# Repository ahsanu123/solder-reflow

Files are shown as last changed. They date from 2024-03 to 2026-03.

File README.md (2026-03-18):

<h1 align="center">🌕 SORE V3 - Prototype 1</h1> 
<p align="center">
  <a href="https://github.com/ahsanu123/solder-reflow"> 
   
  </a>
</p>

<p align="center">
  <a href="">
    
  </a>
  <a href="">
    
  </a>
  <a href="">
    
  </a>
  <a href="https://github.com/ahsanu123/solder-reflow/blob/main/LICENSE">
    
  </a>
</p>

## ✏️ SORE - Solder Reflow

🌕 SORE - Solder Reflow,  DIY hot plate use PT100 for temperature sensor controlled with ESP32-S3,
with TFT LCD, programmed in 🦀 Rust with [Slint](https://slint.dev/) as user interface

> Designed With [KICAD](https://www.kicad.org)

<p align="center" style="background-color: white;">
schematic
</p>

## 🏆 WIP For Version 3

> [!NOTE]
> - use esp32-s3
> - use usb jtag and usb serial 
> - try to use power supply module instead of using external adaptor, [Hi-Link](https://www.tokopedia.com/eltech-online/hi-link-3-3v-5v-9v-12v-24v-hi-link-ling-hlk-ac-to-dc-isolation-power-supply-unit-switching-module-catu-daya-adaptor-trafo-all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)
> - add generic lcd spi connector instead of spesific display pinout.
> - use [Slint](https://slint.dev/) for user interface
> - think about how to stack the heater so its not separated, model it with inventor
> - if possible, buy local component only

<details>
 <summary>Sketch</summary>
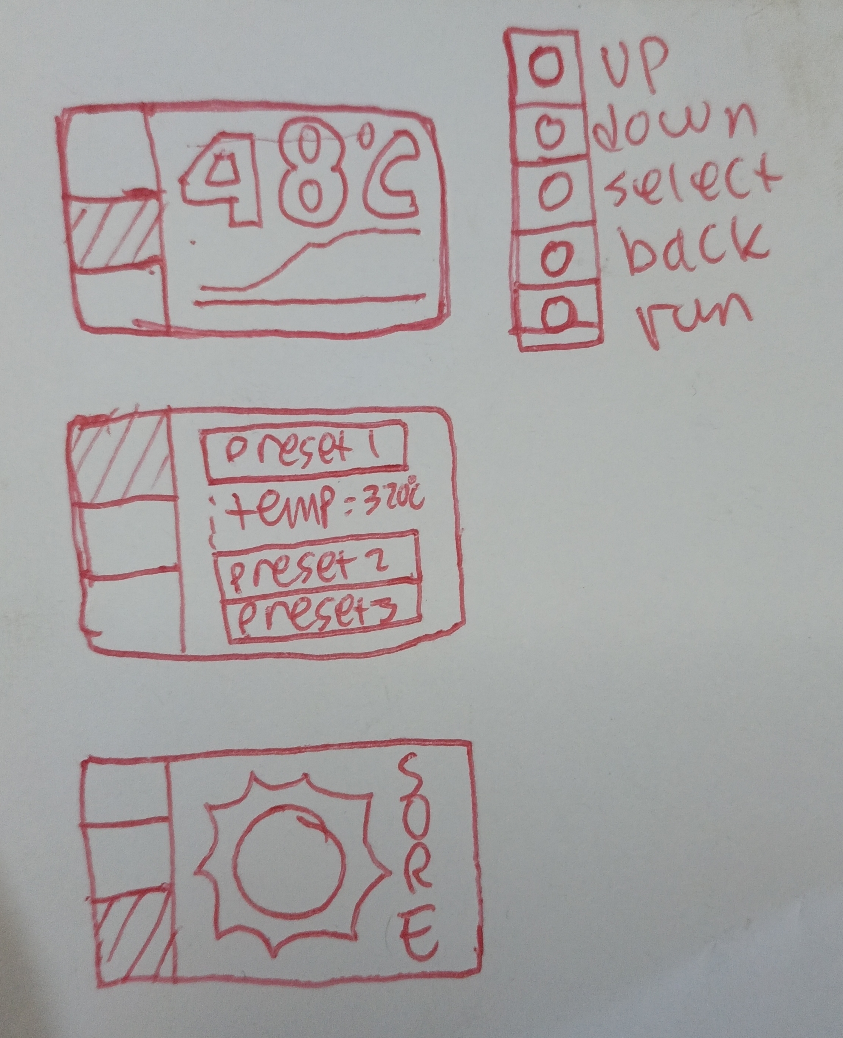
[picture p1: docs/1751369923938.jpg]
  
</details>
 
## 🖍️ Plot of Sampled Data

<details>
 <summary>
  Plot Collection
 </summary>
 
- multiple sampling at 2Mhz (except first one)
signal was moving averaged filter, first graph was actually noisy, and rest was actually not really noisy, but after filtered low noise signal look bumped
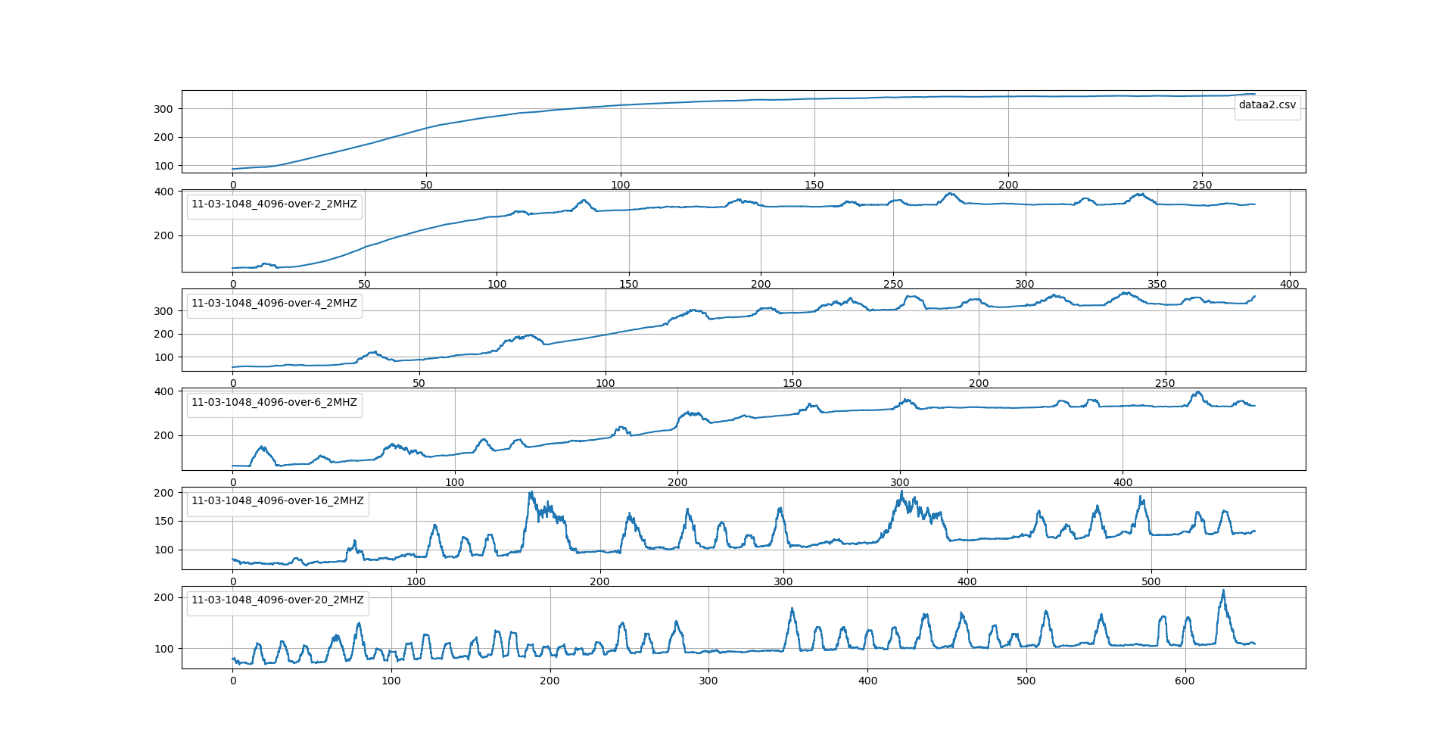
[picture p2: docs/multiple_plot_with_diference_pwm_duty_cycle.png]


- Transfer Function Estimation
$`y(t) = 350(1-e^{(t-d)/tau})`$ in temperature degre (celcius), d = 17.5 second
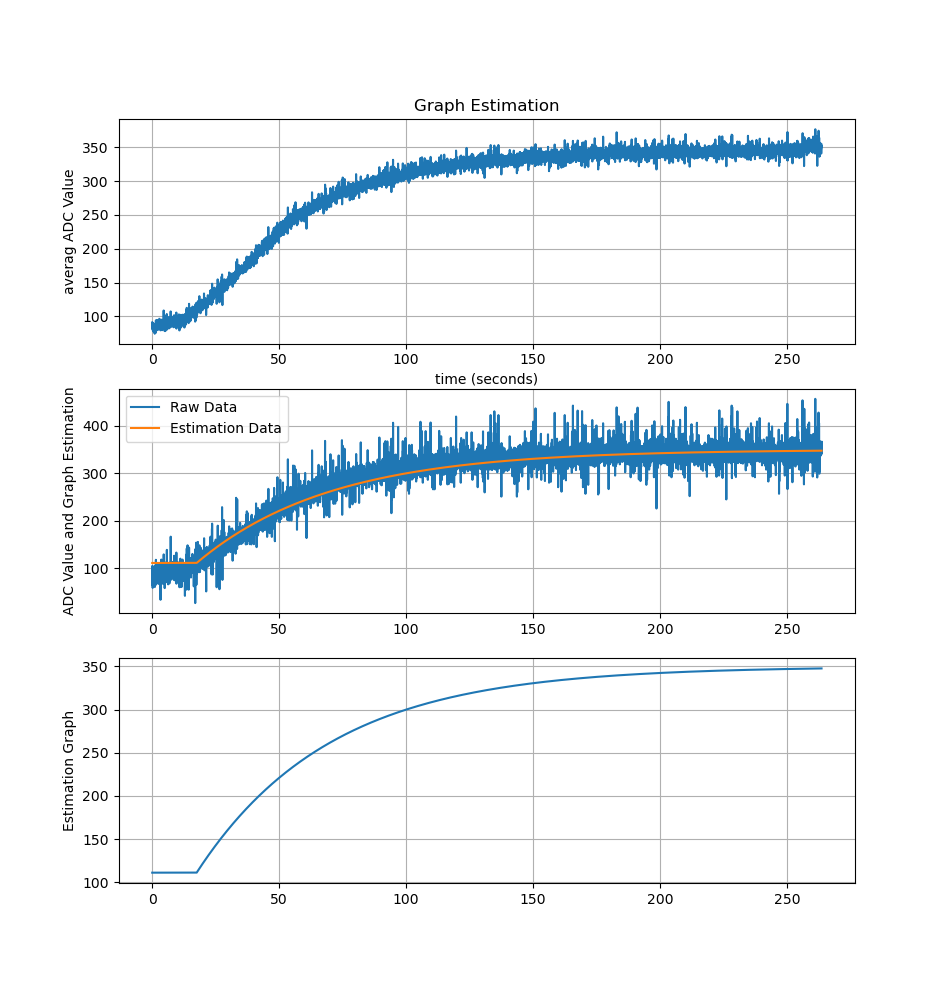
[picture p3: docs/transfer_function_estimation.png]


- first time sampled diagram [30 oktober 2024]


</details>

## 🌱 V3 Project Progress

<details>
 <summary>
  Expand To See Progress.
 </summary> 
  
 **Version 2**
- PCB Design Finished 10 june 2024 20:51
- Order _BOM_ and PCB
- PCB and BOM Arrive 12 july 2024 about 16:00
- Start to soldering 13 july 2024 about 06:00 (**weekend**)
- make adc class to simplify adc initialization 23 july 2024 at 21:21
- Check Out GPIO (Worked!!😃) 26 july 2024 at 22:24
- Try to use JLink for jtag debugging, but fail 😞 , 27 july 2024 at 17:30
- Try again to use JLink for jtag debugging, Worked!! 😃 , 28 july 2024 at 11:36
- Add `Button` class to add Input with callback, 29 Agustus 2024 at 19:42
- ⚠️ turn out, TL074 (not TL074xH) need minimum 10v to operate and not single supply quad opamp 😞, fortunately there is LM324 (same package and single supply support), currently still in shipping, need to wait if it really work or not, 01 september 2024 at 18:05
- ✔️ ok LM324 worked, currently still investigate why adc are really noisy, 03 september 2024 at 13:34
- looks ESP32 IDF adc getting more stable if `frequency` increased, try to use 20Khz but its not stable, but use 1Mhz its more stable 14 september 2024 at 21:00
- ✔️ LVGL worked but task semaphore block update of LVGL (still investigate), 05 oktober 2024 at 10:13
- ✔️ now LVGL with Button input worked!! 😃, need learn more how to map LVGL key to input button, 05 oktober 2024 at 13:23
- ✔️ sampling data from heater and plot it, 30 oktober 2024 at 2015

**Version 3**
- ⏰ 11 June 2025 19:31, make it version 3,
- ⏰ 14 September 2025 12:57, complete basic pcb component placement.
- ⏰ 14 September 2025 17:59, after searching for **Random turn on SSR** (non Zero Crossing) on local market, i cant find easy to buy device, so i will stick to use zero crossing ssr and will count for zero crossing with **H11AA1** and determine how long to turn on and turn off.

- ⏰ 15 March 2026, able to run slint on ESP32S3 on `temperature-measurement-dongle`

</details>

## 🌴 Reference 

- Slint on Mcu platform sample docs -> https://github.com/slint-ui/slint/blob/master/examples/mcu-board-support/README.md
- Slint MCU support Discussion -> https://github.com/slint-ui/slint/discussions/5008
- Slint MCU Template (raspi pico) -> https://github.com/slint-ui/slint-mcu-rust-template/blob/main/src/main.rs
- Slint Linux Template (Linux, etc) -> https://github.com/slint-ui/slint-rust-template/tree/main
- Slint ESP32 Example -> https://github.com/slint-ui/slint/blob/master/examples/mcu-board-support/esp32_s3_box_3.rs
- SSR Phidgets -> https://www.phidgets.com/docs/Solid_State_Relay_Guide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

<sup> Work In Progress Version 3 for 2025 🔥, Made with ♥️ by AH... </sup>

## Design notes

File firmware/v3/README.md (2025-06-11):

## Note 

- `esp-generate --chip esp32 -o alloc -o embassy -o defmt -o unstable-hal Sore-v3`

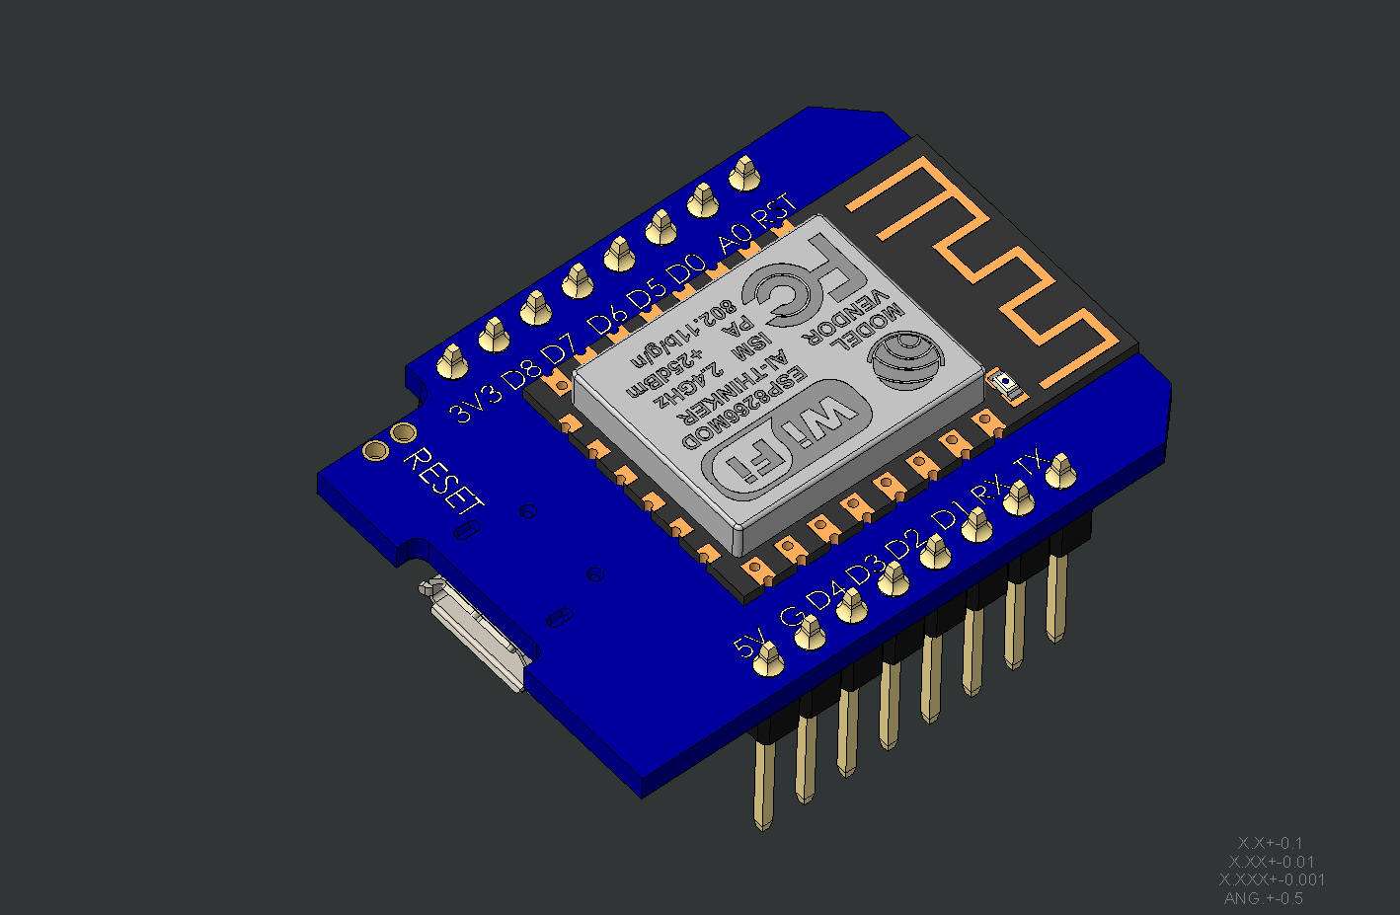
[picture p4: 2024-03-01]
hardware/v2/downloadedLibrary/wemos-mini-d1.png

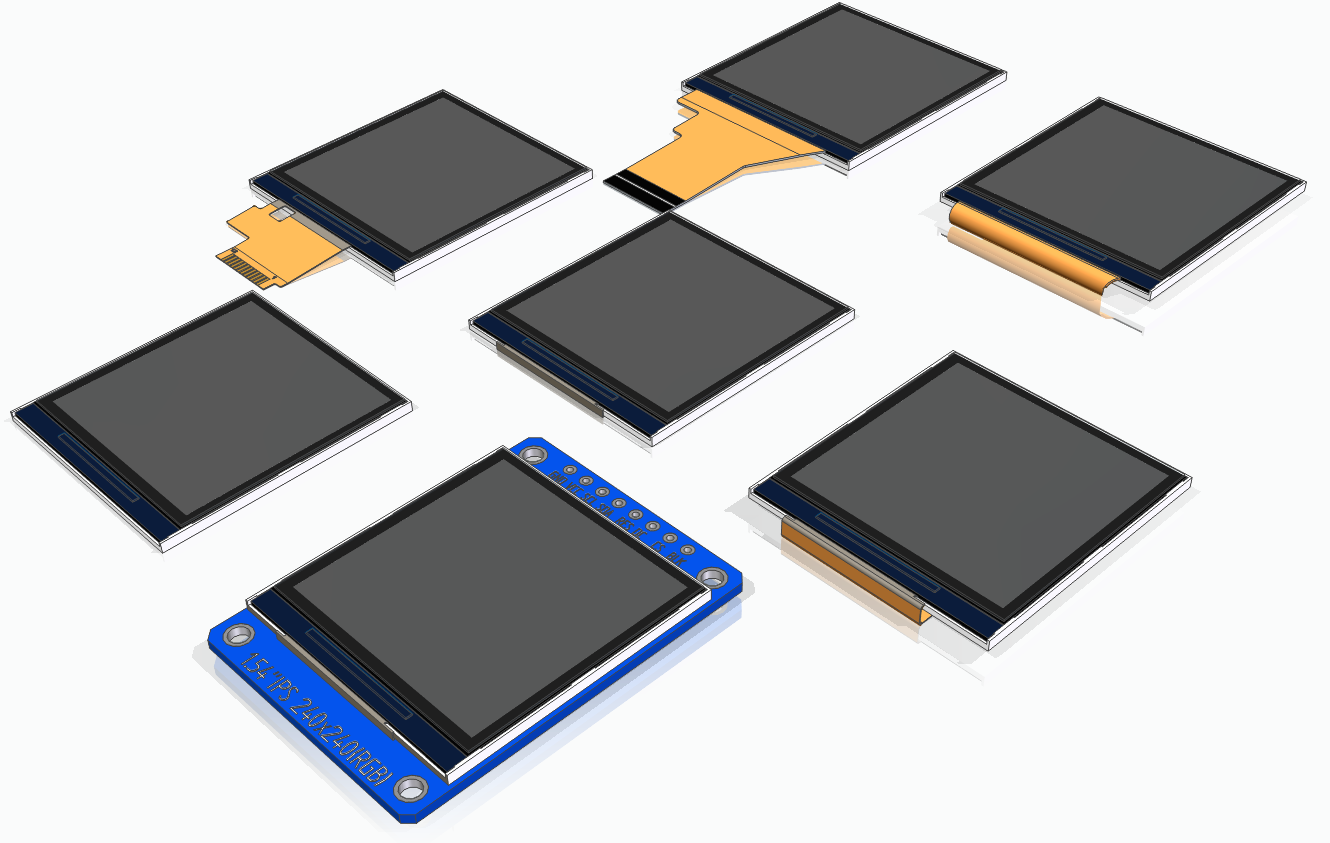
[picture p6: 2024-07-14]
hardware/v2/downloadedLibrary/Capture.PNG

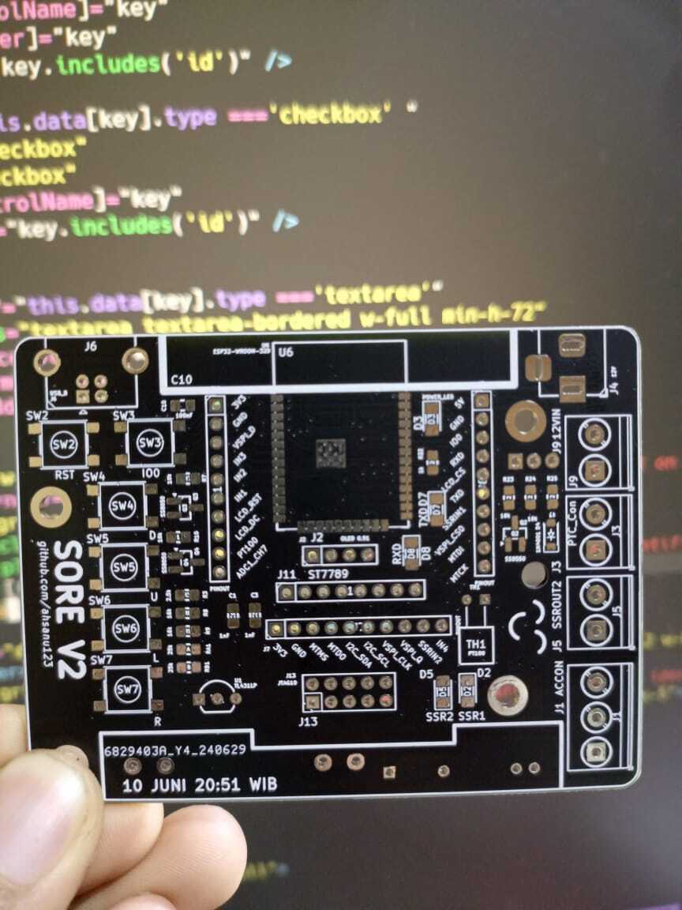
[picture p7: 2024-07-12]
docs/Sudi-pic1.jpg

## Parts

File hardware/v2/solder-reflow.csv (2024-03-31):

Item | Qty | Reference(s) | Value | LibPart | Footprint | Datasheet | DNP | Availability | Check_prices | Description | MANUFACTURER | MF | MP | PARTREV | Package | Price | STANDARD | Sim.Device | Sim.Enable | Sim.Pins | SnapEDA_Link
1 | 1 | C1 | 68nF | Device:C | Capacitor_THT:C_Disc_D4.3mm_W1.9mm_P5.00mm | ~ |  |  |  |  |  |  |  |  |  |  |  |  | 0
2 | 1 | C2 | 390nF | Device:C | Capacitor_THT:C_Disc_D4.3mm_W1.9mm_P5.00mm | ~ |  |  |  |  |  |  |  |  |  |  |  |  | 0
3 | 1 | C3 | 180nF | Device:C | Capacitor_THT:C_Disc_D4.3mm_W1.9mm_P5.00mm | ~ |  |  |  |  |  |  |  |  |  |  |  |  | 0
4 | 2 | C4, C5 | 10nF | Device:C | Capacitor_THT:C_Disc_D4.3mm_W1.9mm_P5.00mm | ~ |  |  |  |  |  |  |  |  |  |  |  |  | 0
5 | 1 | C6 | 0.33uF | Device:C_Polarized | Capacitor_THT:CP_Radial_D6.3mm_P2.50mm | ~
6 | 1 | C7 | 0.1uF | Device:C_Polarized | Capacitor_THT:CP_Radial_D6.3mm_P2.50mm | ~
7 | 1 | D1 | 1N4001 | Diode:1N4001 | Diode_THT:D_DO-41_SOD81_P10.16mm_Horizontal | http://www.vishay.com/docs/88503/1n4001.pdf |  |  |  |  |  |  |  |  |  |  |  | D |  | 1=K 2=A
8 | 1 | D2 | SSR | Device:LED | LED_THT:LED_D5.0mm | ~
9 | 1 | D3 | POWER_LED | Device:LED | LED_THT:LED_D5.0mm | ~
10 | 1 | F1 | Fuse | Device:Fuse | Fuse:Fuseholder_Littelfuse_100_series_5x30mm | ~
11 | 5 | H1, H2, H3, H4, H5 | MountingHole_Pad | Mechanical:MountingHole_Pad | MountingHole:MountingHole_3.2mm_M3_DIN965_Pad | ~
12 | 1 | J1 | AC_Con | Connector:Screw_Terminal_01x02 | TerminalBlock_MetzConnect:TerminalBlock_MetzConnect_Type011_RT05502HBWC_1x02_P5.00mm_Horizontal | ~
13 | 1 | J2 | OLED 0.91 | Connector:Conn_01x04_Pin | Connector_PinHeader_2.54mm:PinHeader_1x04_P2.54mm_Vertical | ~
14 | 1 | J3 | PTC_Con | Connector:Screw_Terminal_01x02 | TerminalBlock_MetzConnect:TerminalBlock_MetzConnect_Type011_RT05502HBWC_1x02_P5.00mm_Horizontal | ~
15 | 1 | J4 | Barrel_Jack_Switch_Pin3Ring | Connector:Barrel_Jack_Switch_Pin3Ring | Connector_BarrelJack:BarrelJack_Horizontal | ~
16 | 1 | K1 | G3MB202PDC12 | G3MB202PDC12:G3MB202PDC12 | downloadedLibrary:RELAY_G3MB202PDC12 |  |  | In Stock | https://www.snapeda.com/parts/G3MB-202P-DC12/Omron+Automation+and+Safety/view-part/?ref=eda | Solid State Relays - PCB Mount 12VDC/100-240VAC 2A | Omron | Omron Automation and Safety | G3MB-202P-DC12 | N/A | SIP-4 Omron Automation | None | Manufacturer Recommendation |  |  |  | https://www.snapeda.com/parts/G3MB-202P-DC12/Omron+Automation+and+Safety/view-part/?ref=snap
17 | 1 | Q1 | BC557 | Transistor_BJT:BC557 | Package_TO_SOT_THT:TO-92_Inline_Wide | https://www.onsemi.com/pub/Collateral/BC556BTA-D.pdf
18 | 5 | R1, R2, R4, R5, R6 | 25k | Device:R_US | Resistor_THT:R_Axial_DIN0207_L6.3mm_D2.5mm_P10.16mm_Horizontal | ~ |  |  |  |  |  |  |  |  |  |  |  |  | 0
19 | 1 | R3 | 2.5k | Device:R_US | Resistor_THT:R_Axial_DIN0207_L6.3mm_D2.5mm_P10.16mm_Horizontal | ~ |  |  |  |  |  |  |  |  |  |  |  |  | 0
20 | 3 | R7, R18, R22 | 1k | Device:R_US | Resistor_THT:R_Axial_DIN0207_L6.3mm_D2.5mm_P10.16mm_Horizontal | ~ |  |  |  |  |  |  |  |  |  |  |  |  | 0
21 | 1 | R8 | 17.4k | Device:R_US | Resistor_THT:R_Axial_DIN0207_L6.3mm_D2.5mm_P10.16mm_Horizontal | ~ |  |  |  |  |  |  |  |  |  |  |  |  | 0
22 | 1 | R9 | 107k | Device:R_US | Resistor_THT:R_Axial_DIN0207_L6.3mm_D2.5mm_P10.16mm_Horizontal | ~ |  |  |  |  |  |  |  |  |  |  |  |  | 0
23 | 1 | R10 | 5.1K | Device:R_US | Resistor_THT:R_Axial_DIN0207_L6.3mm_D2.5mm_P10.16mm_Horizontal | ~ |  |  |  |  |  |  |  |  |  |  |  |  | 0
24 | 8 | R11, R14, R15, R16, R17, R19, R20, R21 | 10k | Device:R_US | Resistor_THT:R_Axial_DIN0207_L6.3mm_D2.5mm_P10.16mm_Horizontal | ~ |  |  |  |  |  |  |  |  |  |  |  |  | 0
25 | 1 | R12 | 3.09k | Device:R_US | Resistor_THT:R_Axial_DIN0207_L6.3mm_D2.5mm_P10.16mm_Horizontal | ~ |  |  |  |  |  |  |  |  |  |  |  |  | 0
26 | 1 | R13 | 20k | Device:R_US | Resistor_THT:R_Axial_DIN0207_L6.3mm_D2.5mm_P10.16mm_Horizontal | ~ |  |  |  |  |  |  |  |  |  |  |  |  | 0
27 | 1 | SW1 | RotaryEncoder_Switch | Device:RotaryEncoder_Switch | Rotary_Encoder:RotaryEncoder_Alps_EC11E-Switch_Vertical_H20mm | ~
28 | 1 | TH1 | PT100 | Sensor_Temperature:PT100 | Package_TO_SOT_THT:TO-92-2_Horizontal2 | https://www.heraeus.com/media/media/group/doc_group/products_1/hst/sot_to/de_15/to_92_d.pdf |  |  |  |  |  |  |  |  |  |  |  |  | 0
29 | 1 | U1 | TL431LP | Reference_Voltage:TL431LP | Package_TO_SOT_THT:TO-92_Inline_Wide | http://www.ti.com/lit/ds/symlink/tl431.pdf
30 | 2 | U2, U3 | OPA2134 | Amplifier_Operational:OPA2134 | Package_DIP:DIP-8_W7.62mm_LongPads | http://www.ti.com/lit/ds/symlink/opa134.pdf |  |  |  |  |  |  |  |  |  |  |  |  | 0
31 | 1 | U4 | L7805 | Regulator_Linear:L7805 | Package_TO_SOT_THT:TO-220F-3_Horizontal_TabDown | http://www.st.com/content/ccc/resource/technical/document/datasheet/41/4f/b3/b0/12/d4/47/88/CD00000444.pdf/files/CD00000444.pdf/jcr:content/translations/en.CD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
32 | 1 | U5 | WeMos_D1_mini | MCU_Module:WeMos_D1_mini | Module:WEMOS_D1_mini_light | https://wiki.wemos.cc/products:d1:d1_mini#documentation |  |  |  |  |  |  |  |  |  |  |  |  | 0

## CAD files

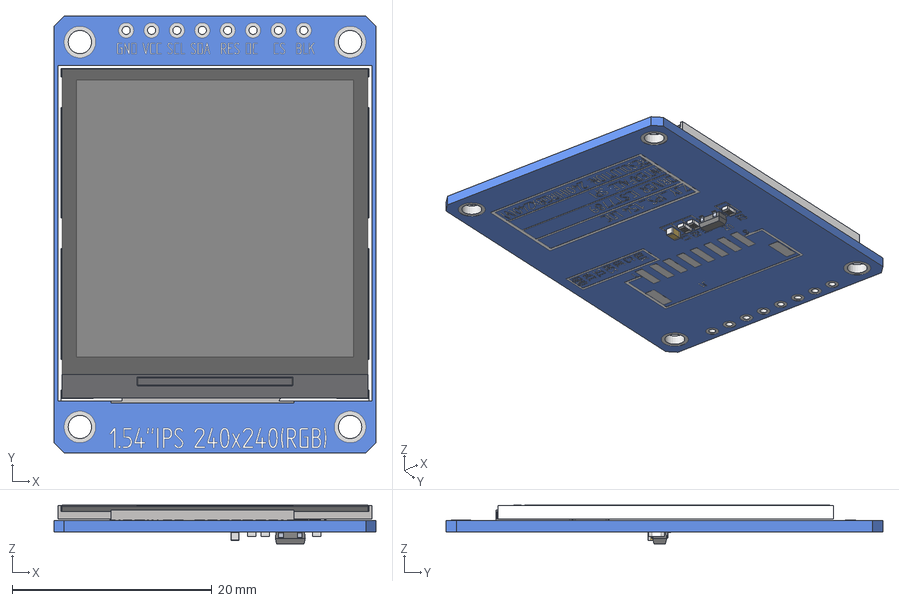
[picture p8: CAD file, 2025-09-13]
hardware/v2/downloadedLibrary/1.54 TFT IPS - Module - Assembly.stp
32.2 x 43.7 x 3.89 mm
1.54 TFT IPS - Module - Board
0603 Resistor x 3
0603 Capacitor
SOT23
1.54 TFT IPS - 12P - Flat Flush Mount

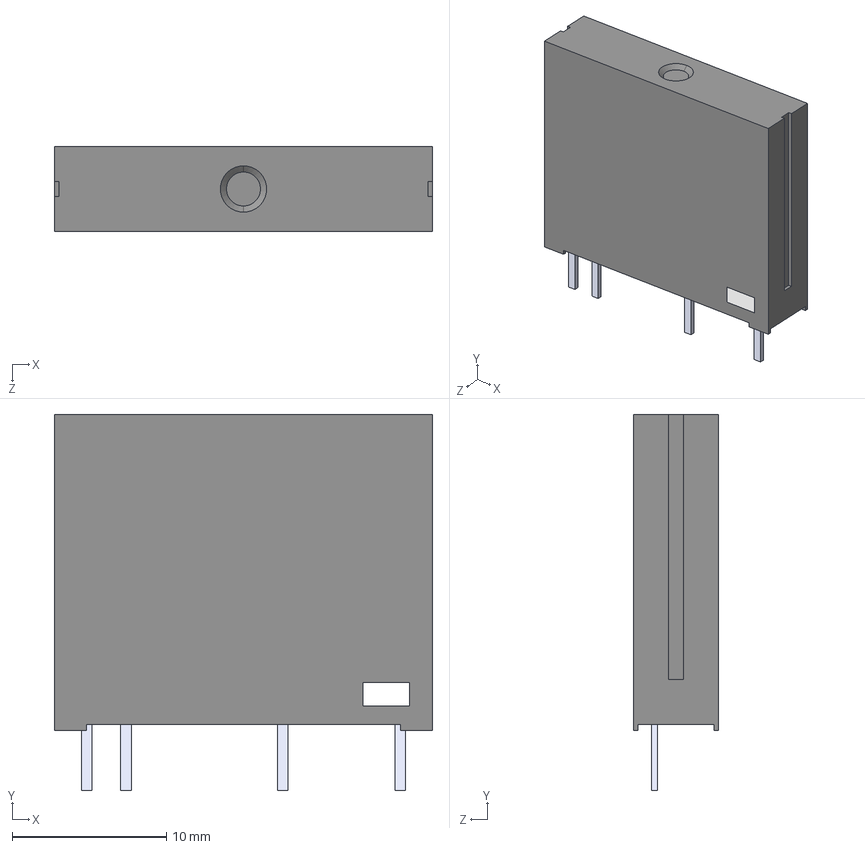
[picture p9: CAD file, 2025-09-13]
hardware/v2/downloadedLibrary/G3MB202PDC12.step
24.5 x 24.4 x 5.50 mm

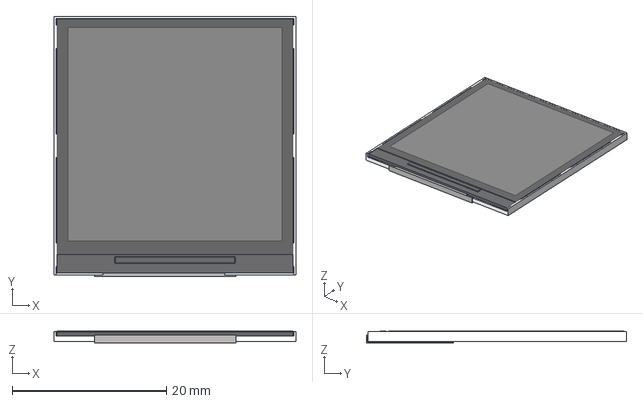
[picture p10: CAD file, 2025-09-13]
hardware/v2/downloadedLibrary/1.54 TFT IPS - 12P - Flat Flush Mount.stp
31.4 x 33.8 x 1.54 mm

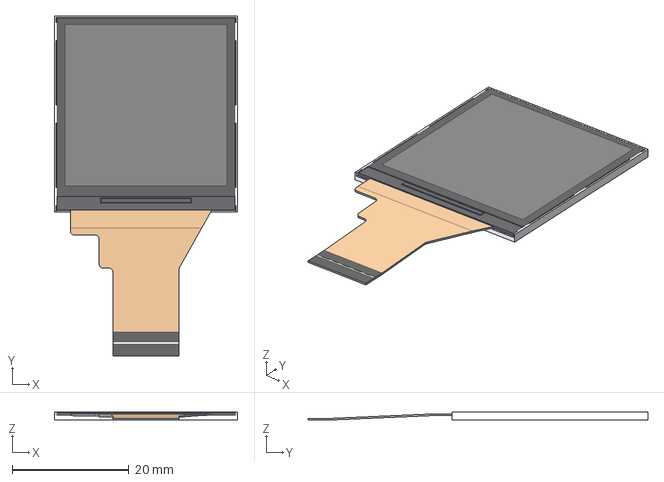
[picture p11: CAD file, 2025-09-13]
hardware/v2/downloadedLibrary/1.54 TFT IPS - 22P - Flat Mount - With Glass.stp
31.4 x 58.3 x 1.37 mm

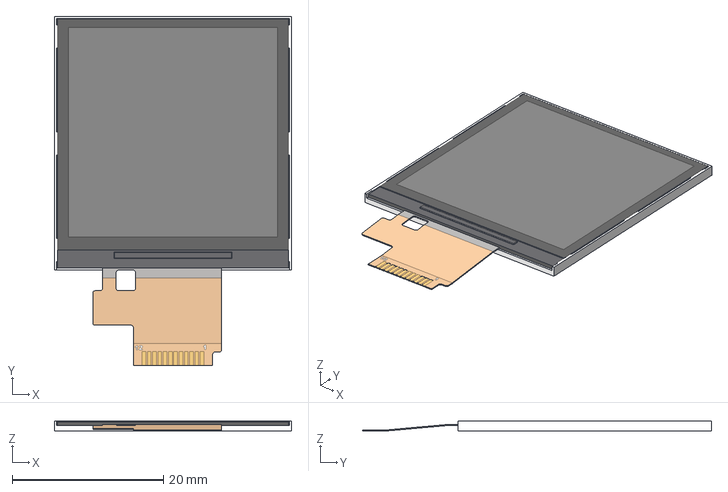
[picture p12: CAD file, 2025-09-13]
hardware/v2/downloadedLibrary/1.54 TFT IPS - 12P - Flat Mount.stp
31.4 x 46.2 x 1.37 mm

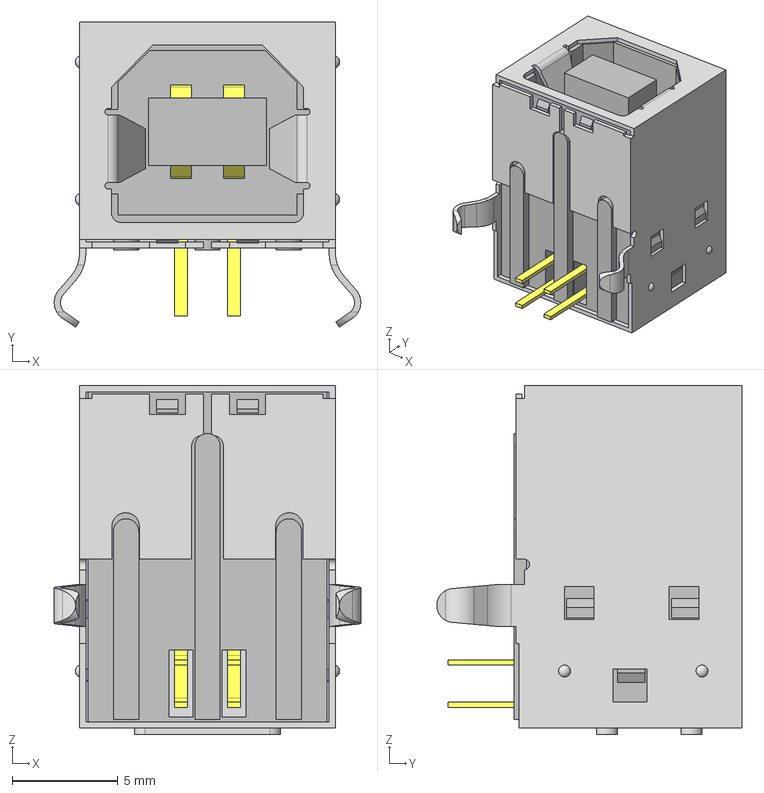
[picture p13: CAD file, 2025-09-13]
hardware/v2/downloadedLibrary/USB-B-S-F-B-TH.stp
14.5 x 14.4 x 16.5 mm
USB-B-S-TH_S
USB-B-S-B-TH_B
USB-B-S-TH_P

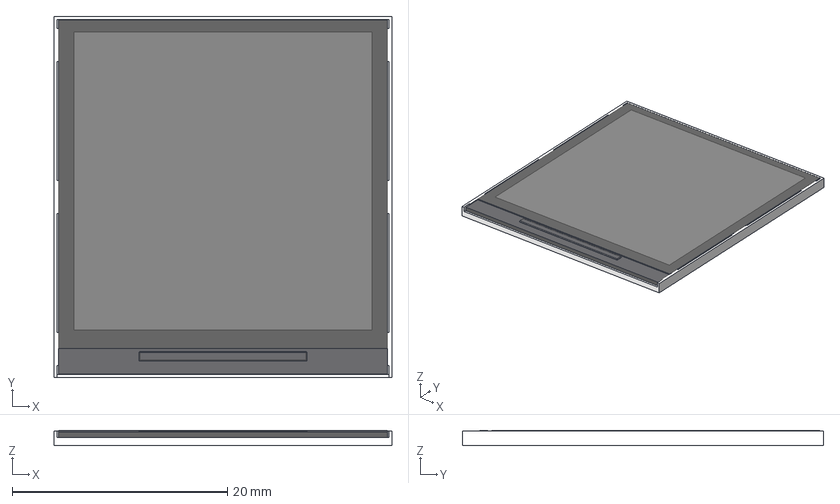
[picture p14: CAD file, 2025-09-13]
hardware/v2/downloadedLibrary/1.54 TFT IPS - No Cable.stp
31.4 x 33.6 x 1.37 mm

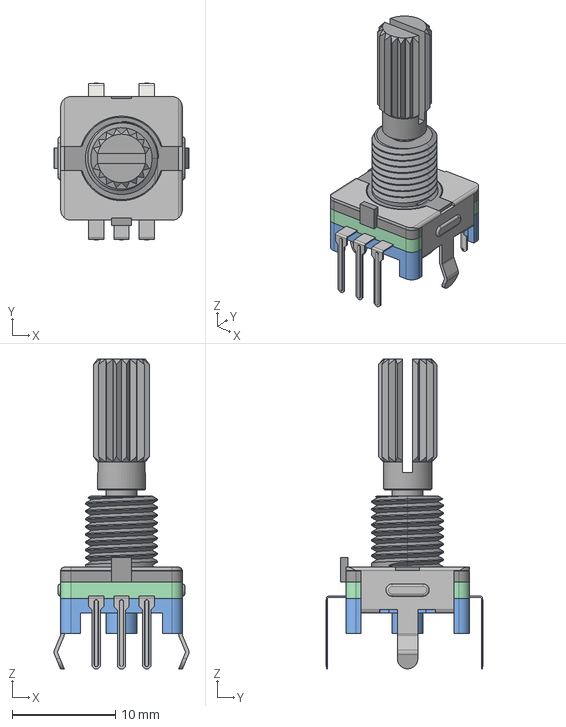
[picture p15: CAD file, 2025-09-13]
hardware/v2/downloadedLibrary/EC11_Rotary_Encoder_Switched.step
13.1 x 15.3 x 30.1 mm

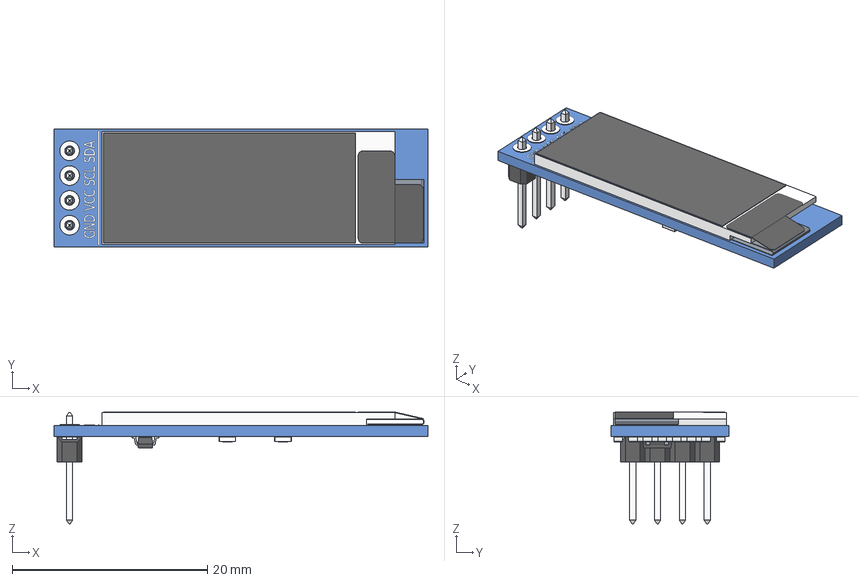
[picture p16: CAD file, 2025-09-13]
hardware/v2/downloadedLibrary/OLED_0.91_128x32.stp
38.3 x 12.1 x 11.5 mm
OLED_0.91_128x32
Pin Header 4 x 1 TH 2.54mm Pitch
RESC-0603 x 13
2SD0601A

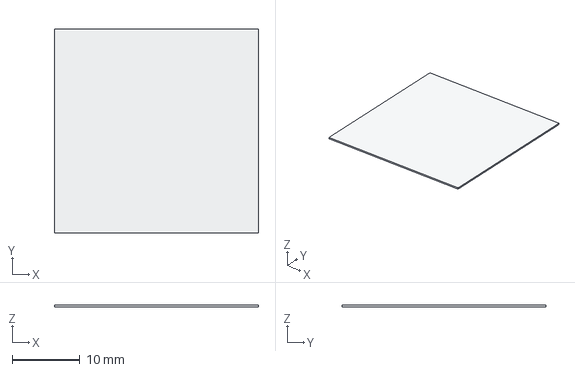
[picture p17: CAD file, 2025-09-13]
hardware/v2/downloadedLibrary/1.54 TFT IPS - Glass.stp
30.1 x 30.1 x 0.279 mm

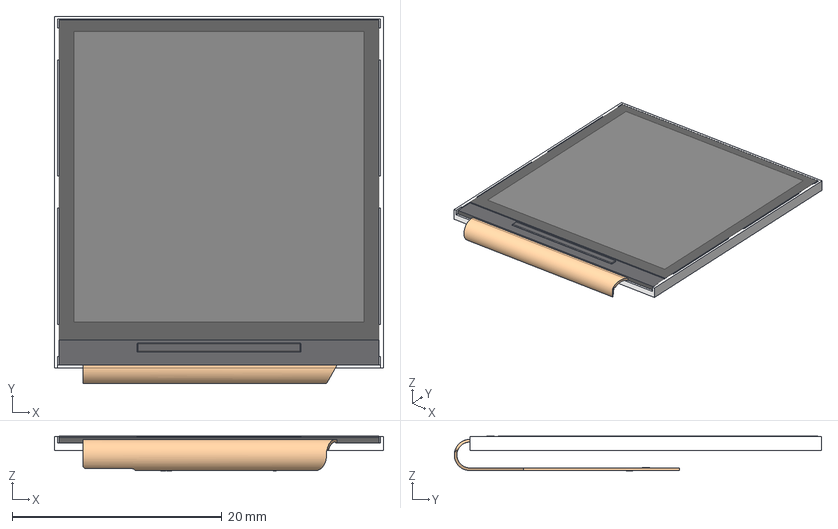
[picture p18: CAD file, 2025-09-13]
hardware/v2/downloadedLibrary/1.54 TFT IPS - 22P - Reverse Mount - With Glass.stp
31.4 x 35.1 x 3.30 mm

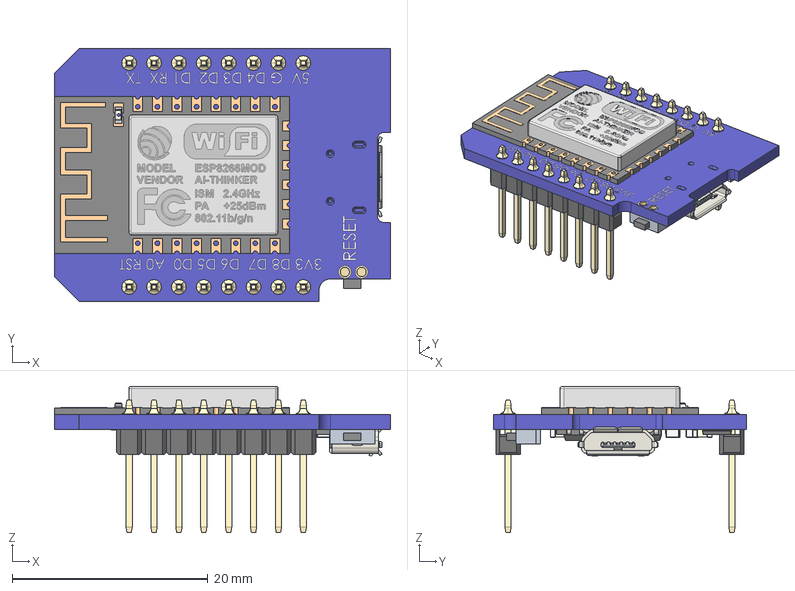
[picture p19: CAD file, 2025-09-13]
hardware/v2/downloadedLibrary/wemos-mini-d1.stp
34.3 x 25.8 x 14.9 mm
PRODUCT_146_ASM_2
PRODUCT_260_3
PRODUCT_323_ASM_2
RES_0805_1 x 12
CAP_0805_1 x 7
SOT23_1_1 x 2
SOT23_2_1 x 2
SOT23_3_1 x 2
SOT23_001_1 x 2
SOT23-5_1
SOT23-5_001_1_1
SOT23-5_001_2_1
SOT23-5_001_3_1
SOT23-5_001_4_1
SOT23-5_001_5_1
SOD-323_1
SOIC-16_150MIL_1
SOIC-16_150MIL_001_1_1
SOIC-16_150MIL_001_2_1
SOIC-16_150MIL_001_3_1
SOIC-16_150MIL_001_4_1
SOIC-16_150MIL_001_5_1
SOIC-16_150MIL_001_6_1
SOIC-16_150MIL_001_7_1
SOIC-16_150MIL_001_8_1
SOIC-16_150MIL_001_9_1
SOIC-16_150MIL_001_10_1
SOIC-16_150MIL_001_11_1
SOIC-16_150MIL_001_12_1
SOIC-16_150MIL_001_13_1
SOIC-16_150MIL_001_14_1
SOIC-16_150MIL_001_15_1
SOIC-16_150MIL_001_16_1
COMPONENTS_2_11__2
_PUSH_BUTTON_-_IMPORTIERT1__2
_USB_SOCKET_-_IMPORTIERT1__2
PCB_2
PIN x 16

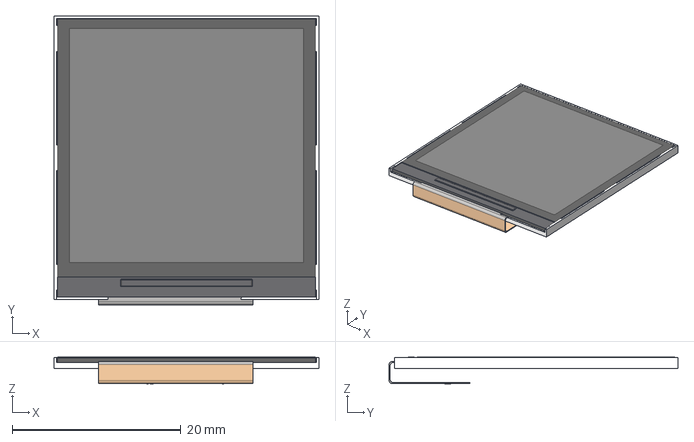
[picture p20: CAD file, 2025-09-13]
hardware/v2/downloadedLibrary/1.54 TFT IPS - Reverse Mount.stp
31.4 x 34.2 x 3.16 mm

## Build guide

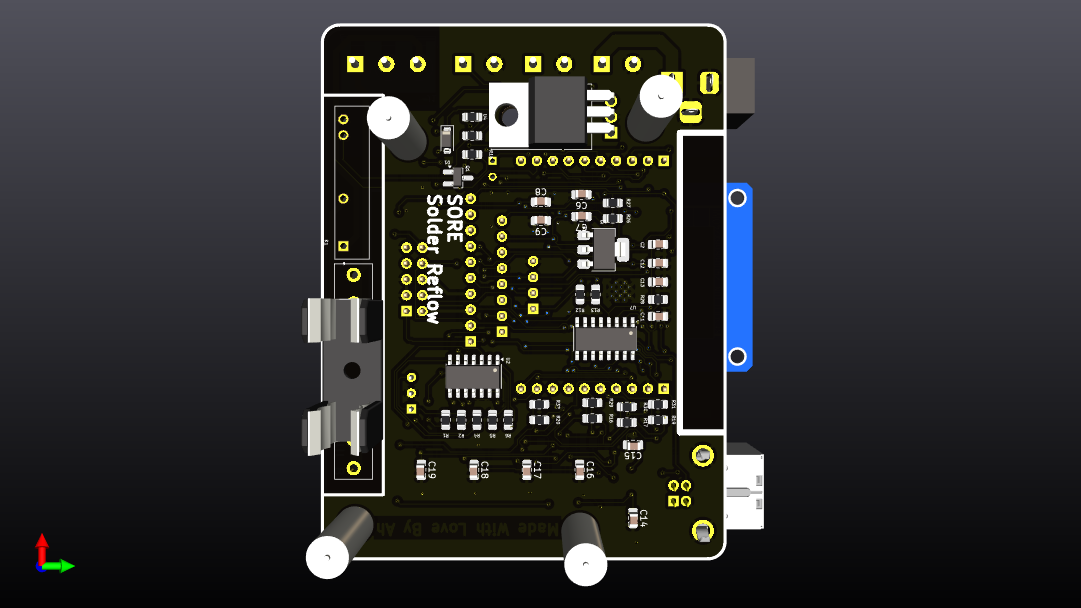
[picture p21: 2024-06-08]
docs/solder-reflow-pcb-back-v2.png

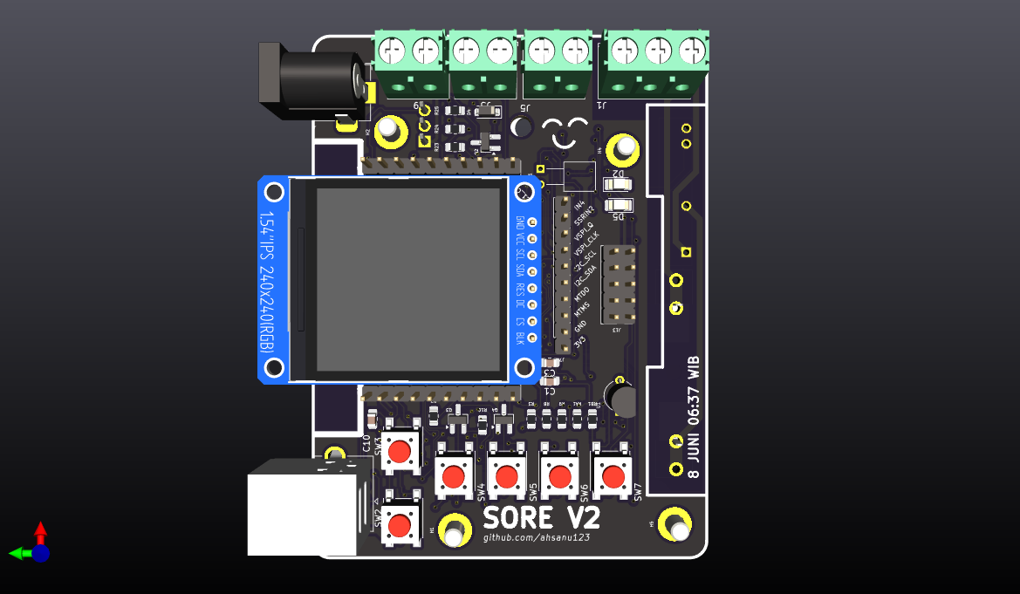
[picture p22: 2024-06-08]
docs/solder-reflow-pcb-v2.png

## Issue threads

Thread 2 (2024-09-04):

ADC Reading Is To Noisy, but Oscilloscope reading seem good

ahsanu123, 2024-09-04:
investigate why adc reading are too noisy,

ahsanu123, 2024-11-20:
solved, if sampled on 20kHz data is noisy, but if data filtered with moving averaged, its quite smooth. but if use sampling frequency 1MHz or above, sampled data not noisy, but after moving averaged filter, data become bumped

Closed 2024-11-20.

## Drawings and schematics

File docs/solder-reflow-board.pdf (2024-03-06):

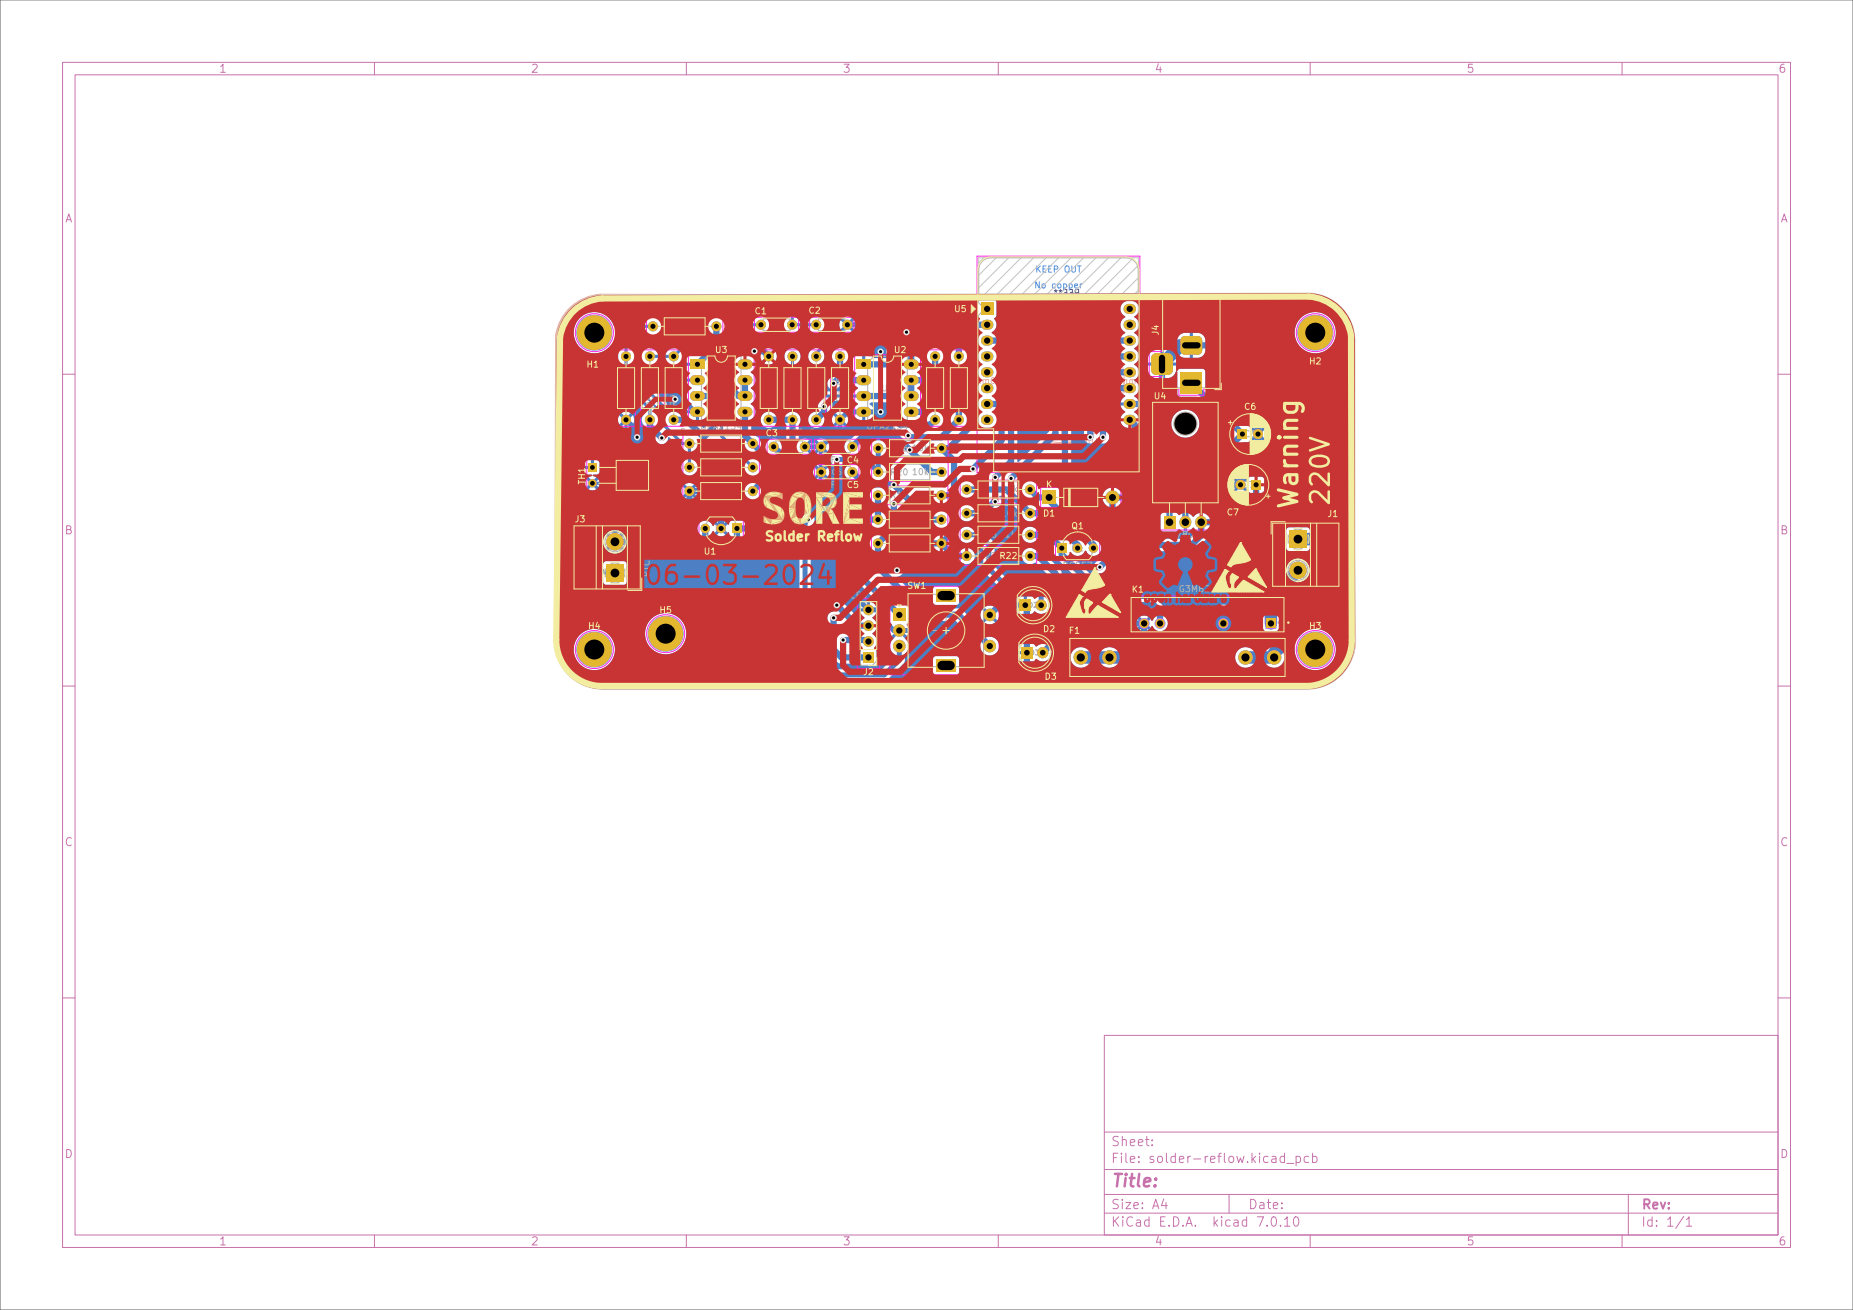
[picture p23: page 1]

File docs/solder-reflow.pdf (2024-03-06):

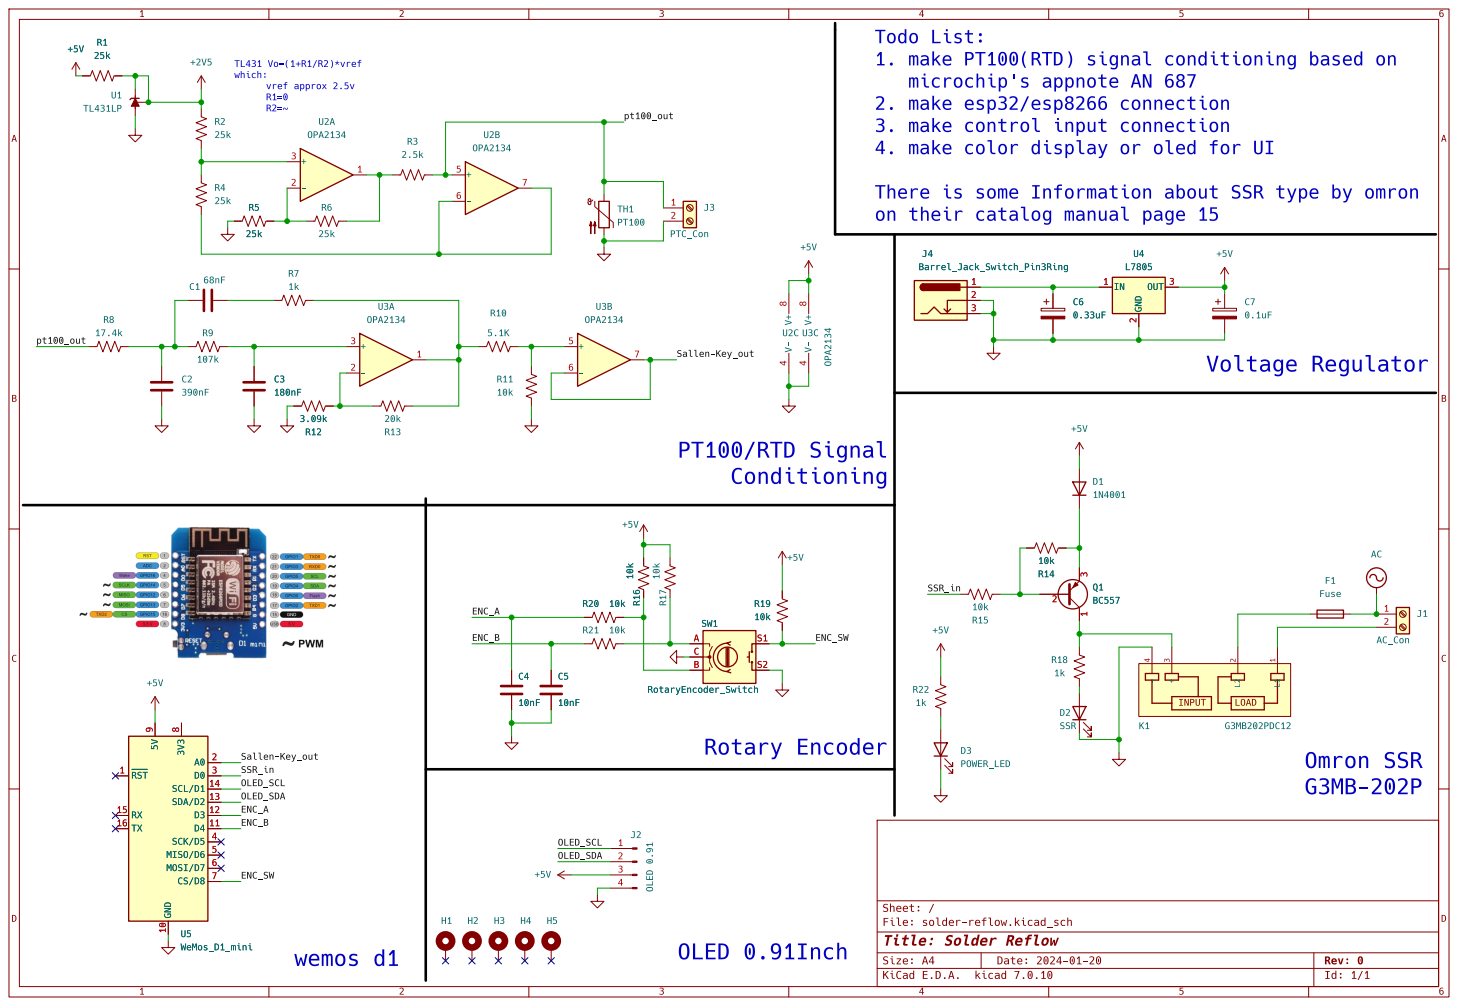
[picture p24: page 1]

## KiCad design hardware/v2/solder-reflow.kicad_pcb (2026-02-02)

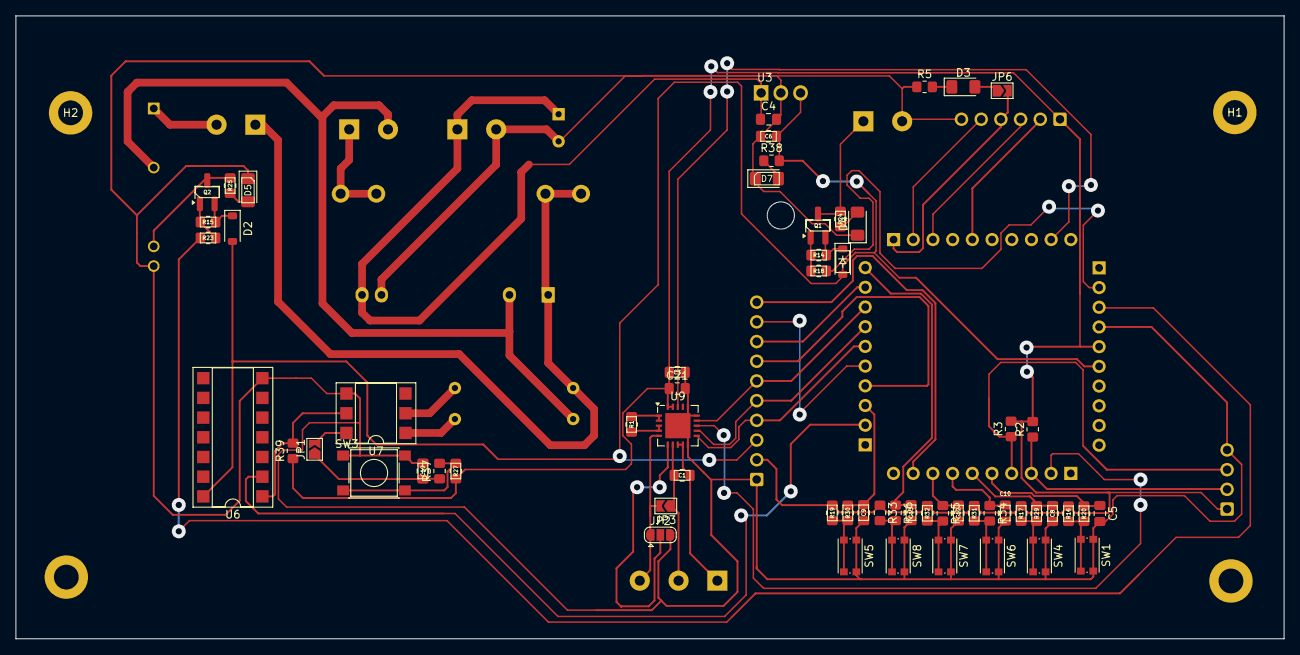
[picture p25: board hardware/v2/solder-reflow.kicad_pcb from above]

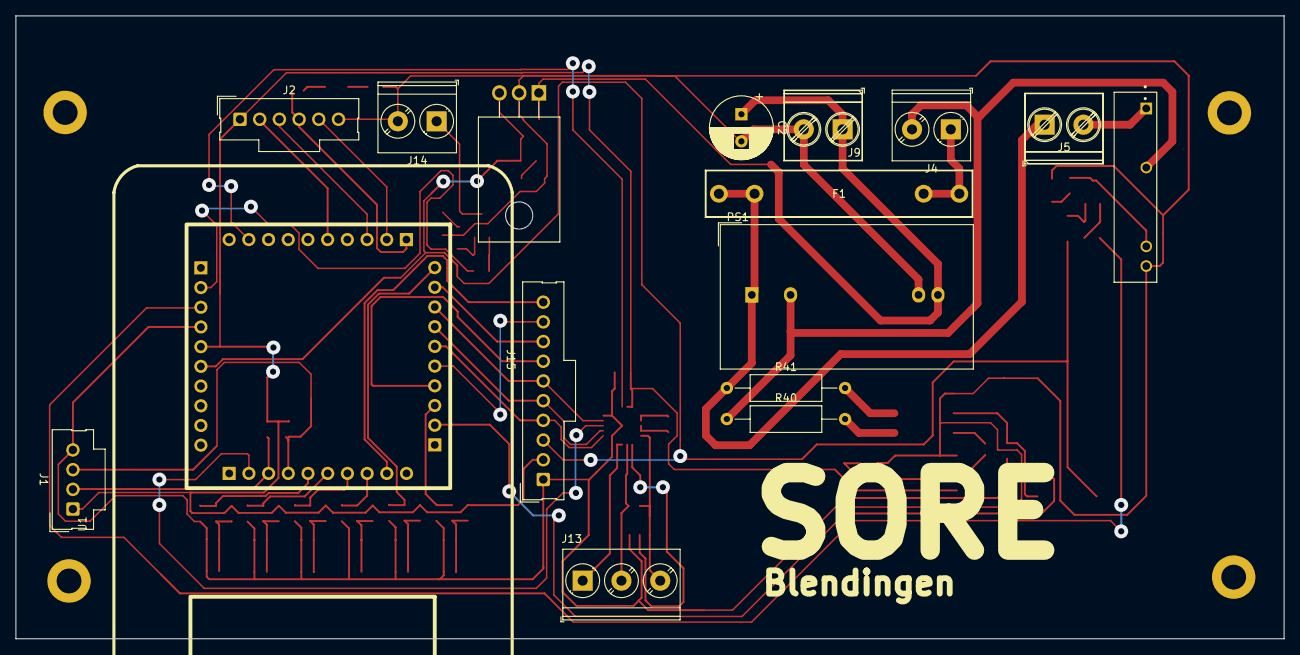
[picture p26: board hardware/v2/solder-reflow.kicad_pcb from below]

Board: 2 copper layers, 163.5 x 80.3 mm, 80 parts (16 on the bottom side), 61 nets.

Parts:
C1, C3, C21: 100nF; C_0805_2012Metric_Pad1.18x1.45mm_HandSolder
C2: 100uF/16V; CP_Radial_D8.0mm_P3.50mm
C4: 0.33uF; C_0805_2012Metric_Pad1.18x1.45mm_HandSolder
C5, C8, C9, C10, C12, C13, C19: 1uF; C_0805_2012Metric_Pad1.18x1.45mm_HandSolder
C6: 0.1uF; C_0805_2012Metric_Pad1.18x1.45mm_HandSolder
D1, D2: 1N4001; D_SOD-123
D3: Indicator; LED_1206_3216Metric_Pad1.42x1.75mm_HandSolder
D4: SSR2; LED_1206_3216Metric_Pad1.42x1.75mm_HandSolder
D5: SSR1; LED_1206_3216Metric_Pad1.42x1.75mm_HandSolder
D7: POWER_LED; LED_1206_3216Metric_Pad1.42x1.75mm_HandSolder
F1: Fuse; Fuseholder_Littelfuse_100_series_5x30mm
H1, H2, H3, H4: MountingHole_Pad; MountingHole_3.2mm_M3_DIN965_Pad
J1: I2C; Molex_SL_171971-0004_1x04_P2.54mm_Vertical
J2: I2S; Molex_SL_171971-0006_1x06_P2.54mm_Vertical
J4: 220V; TerminalBlock_Phoenix_PT-1,5-2-5.0-H_1x02_P5.00mm_Horizontal
J5: HEATER; TerminalBlock_Phoenix_PT-1,5-2-5.0-H_1x02_P5.00mm_Horizontal
J9: 12VIN; TerminalBlock_Phoenix_PT-1,5-2-5.0-H_1x02_P5.00mm_Horizontal
J13: RTD_PT100; TerminalBlock_Phoenix_PT-1,5-3-5.0-H_1x03_P5.00mm_Horizontal
J14: SSROUT2; TerminalBlock_Phoenix_PT-1,5-2-5.0-H_1x02_P5.00mm_Horizontal
J15: LCD_CONN; Molex_SL_171971-0010_1x10_P2.54mm_Vertical
JP1: InH11AA1; SolderJumper-2_P1.3mm_Open_TrianglePad1.0x1.5mm
JP2: 3_OR_2_Wire; SolderJumper-3_P1.3mm_Open_RoundedPad1.0x1.5mm
JP3, JP6: 2_Wire; SolderJumper-2_P1.3mm_Open_TrianglePad1.0x1.5mm
K1: G3MB202PDC12; RELAY_G3MB202PDC12
PS1: HLK-2M12 12V 2W; Converter_ACDC_Hi-Link_HLK-2Mxx
Q1, Q2: SS8550; SOT-23_Handsoldering
R1: 400 1%; R_0805_2012Metric_Pad1.20x1.40mm_HandSolder
R2, R3: 4K7; R_0805_2012Metric_Pad1.20x1.40mm_HandSolder
R5: 1K; R_0805_2012Metric_Pad1.20x1.40mm_HandSolder
R14, R15, R16, R17, R18, R19, R23, R27, R31, R32, R33, R39: 10k; R_0805_2012Metric_Pad1.20x1.40mm_HandSolder
R20, R29, R30, R34, R35, R36, R37: 22k; R_0805_2012Metric_Pad1.20x1.40mm_HandSolder
R24, R25, R38: 1k; R_0805_2012Metric_Pad1.20x1.40mm_HandSolder
R40, R41: 10k 1W; R_Axial_DIN0309_L9.0mm_D3.2mm_P15.24mm_Horizontal
SW1: L; SW_Push_1P1T_NO_CK_KMR2
SW3: SWH11AA1; SW_Push_1P1T_NO_6x6mm_H9.5mm
SW4: D; SW_Push_1P1T_NO_CK_KMR2
SW5: U; SW_Push_1P1T_NO_CK_KMR2
SW6, SW7, SW8: R; SW_Push_1P1T_NO_CK_KMR2
U1: ESP32-S3-Tempel; esp32-s3-tempel
U3: L7805; TO-220F-3_Horizontal_TabDown
U6: 74LS14; DIP-14_W7.62mm_SMDSocket_SmallPads
U7: H11AA1; DIP-6_W7.62mm_SMDSocket_SmallPads
U9: MAX31865xTP; TQFN-20-1EP_5x5mm_P0.65mm_EP3.25x3.25mm

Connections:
+3.3V: C3.1, C21.1, J1.1, J2.1, J15.2, R2.2, R3.2, R16.1, R17.1, R19.1, R27.1, R31.1, R32.1, R33.1, R39.1, U1.35 (3V3), U9.19 (DVDD), U9.20 (VDD)
+5V: C6.1, D1.2 (A), D2.2 (A), J15.3, R38.2, U1.36 (5V), U3.3 (OUT), U6.14 (VCC)
+12V: C2.1, C4.1, J9.1, PS1.4 (+Vout), U3.1 (IN)
/BCLK: J2.3, U1.23 (IO45)
/CS0: J15.9, U1.15 (IO10)
/DIO: J2.5, U1.22 (IO48)
/I2C_SCL: J1.3, R3.1, U1.4 (IO7)
/I2C_SDA: J1.2, R2.1, U1.3 (IO6)
/IN1: C5.1, R20.1, U1.5 (IO15)
/IN2: C8.1, R29.1, U1.6 (IO16)
/IN3: C9.1, R30.1, U1.13 (IO46)
/IN4: C10.1, R34.1, U1.7 (IO17)
/IN5: C12.1, R35.1, U1.8 (IO18)
/IN6: C13.1, R36.1, U1.20 (IO21)
/IO5: U1.2 (IO5), U9.13 (~CS)
/IO8: J15.10, U1.9 (IO8)
/IO42: U1.29 (IO42), U9.18 (~DRDY)
/MCLK: J2.2, U1.25 (IO38)
/MISO: J15.6, U1.18 (IO13), U9.14 (SDO)
/MOSI: J15.4, U1.16 (IO11), U9.11 (SDI)
/QUADHD: J15.7, U1.14 (IO9)
/QUADWP: J15.8, U1.19 (IO14)
/SCLK: J15.5, U1.17 (IO12), U9.12 (SCLK)
/SSRIN1: R23.1, U1.33 (IO1)
/SSRIN2: R18.1, U1.32 (IO2)
/WS: J2.4, JP6.2 (B), U1.21 (IO47)
/ZC_INPUT: U1.12 (IO3), U6.2
/sw1: R16.2, R20.2, SW1.2
/sw2: R17.2, R29.2, SW4.2
/sw3: R19.2, R30.2, SW5.2
/sw4: R31.2, R34.2, SW6.2
/sw5: R32.2, R35.2, SW7.2
/sw6: R33.2, R36.2, SW8.2
GND: C2.2, C3.2, C4.2, C5.2, C6.2, C8.2, C9.2, C10.2, C12.2, C13.2, C19.2, C21.2, D4.1 (K), D5.1 (K), D7.1 (K), J1.4, J2.6, J9.2, J14.2, J15.1, JP2.3 (B), K1.4 (-), PS1.3 (-Vout), R5.1, SW1.1, SW3.1, SW4.1, SW5.1, SW6.1, SW7.1, SW8.1, U1.34 (GND), U3.2 (GND), U6.7 (GND), U7.4, U9.10 (GND), U9.15 (DGND), U9.16 (GND), U9.21 (GND)
LINE: F1.1, J5.1, PS1.1 (AC/L), R41.1
NEUT: J4.2, K1.2 (L2), PS1.2 (AC/N), R40.1
unnamed: D1.1 (K), Q1.2 (E), R14.2
unnamed: D2.1 (K), Q2.2 (E), R15.2
unnamed: D3.2 (A), JP6.1 (A)
unnamed: D3.1 (K), R5.2
unnamed: D4.2 (A), R24.1
unnamed: D5.2 (A), R25.1
unnamed: D7.2 (A), R38.1
unnamed: F1.2, J4.1
unnamed: J5.2, K1.1 (L1)
unnamed: C1.2, J13.1, U9.8 (RTDIN-), U9.9 (FORCE-)
unnamed: C1.1, J13.2, JP3.1 (A), U9.7 (RTDIN+)
unnamed: J13.3, JP2.1 (A), JP3.2 (B), U9.5 (FORCE+)
unnamed: J14.1, Q1.3 (C), R24.2
unnamed: C19.1, JP1.1 (A), R37.1
unnamed: JP1.2 (B), U7.6
unnamed: JP2.2 (C), U9.6 (FORCE2)
unnamed: K1.3 (+), Q2.3 (C), R25.2
unnamed: Q1.1 (B), R14.1, R18.2
unnamed: Q2.1 (B), R15.1, R23.2
unnamed: R27.2, R37.2, SW3.2
unnamed: R39.2, U6.1, U7.5
unnamed: R40.2, U7.1
unnamed: R41.2, U7.2
unnamed: R1.1, U9.1 (BIAS), U9.2 (REFIN+)
unnamed: R1.2, U9.3 (REFIN-), U9.4 (ISENSOR)

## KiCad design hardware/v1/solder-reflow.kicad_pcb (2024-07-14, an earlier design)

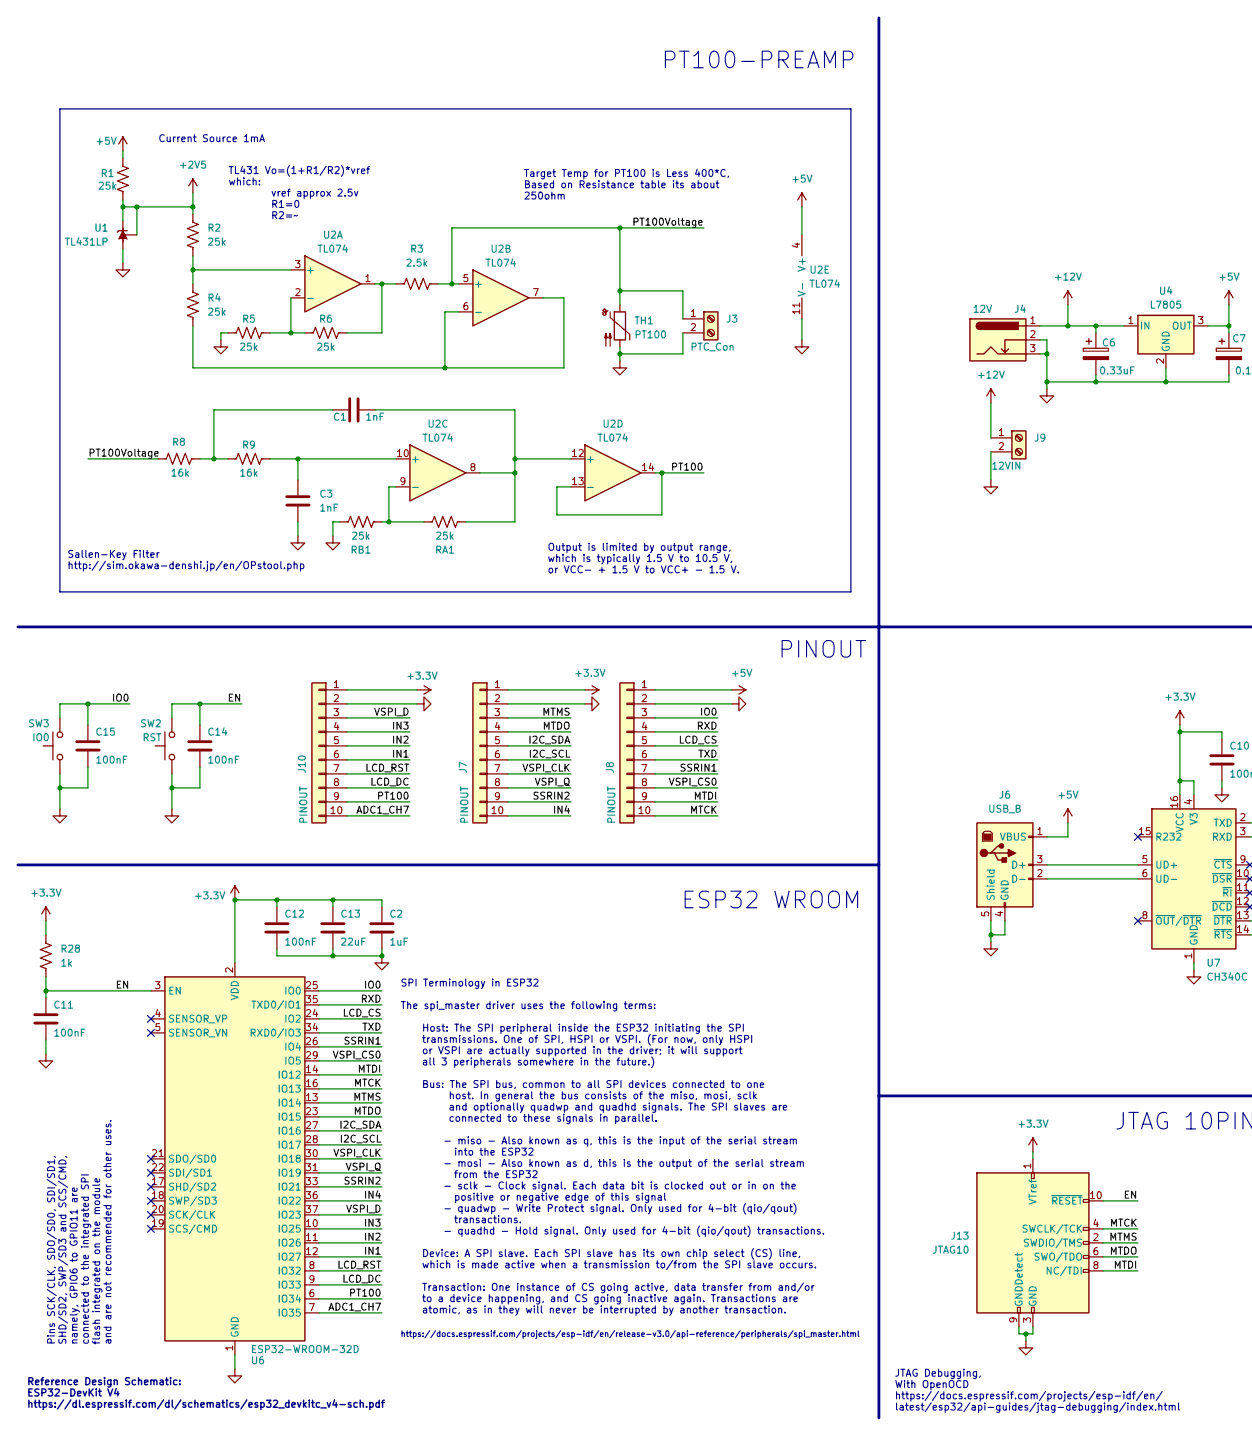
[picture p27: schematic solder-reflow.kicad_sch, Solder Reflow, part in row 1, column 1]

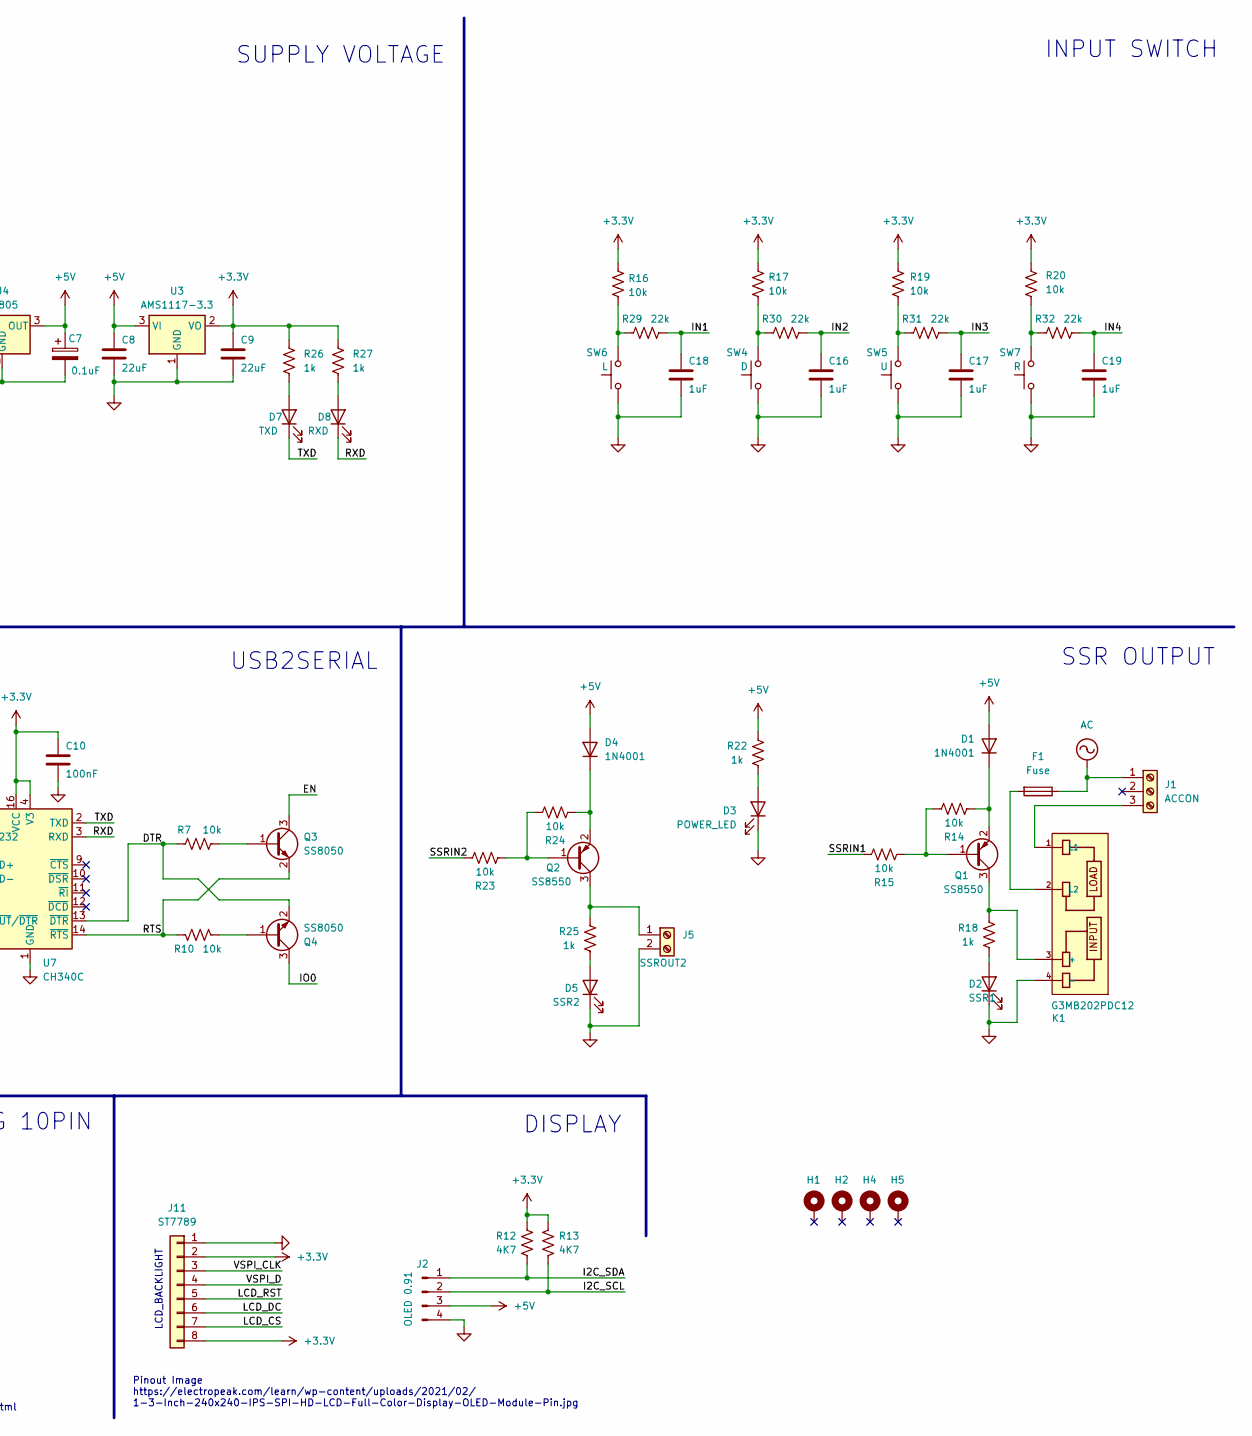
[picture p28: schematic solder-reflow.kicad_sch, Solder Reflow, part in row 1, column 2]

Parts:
C1, C3: 1nF; C_0805_2012Metric_Pad1.18x1.45mm_HandSolder
C2, C16, C17, C18, C19: 1uF; C_0805_2012Metric_Pad1.18x1.45mm_HandSolder
C6: 0.33uF; C_0805_2012Metric_Pad1.18x1.45mm_HandSolder
C7: 0.1uF; C_0805_2012Metric_Pad1.18x1.45mm_HandSolder
C8, C9, C13: 22uF; C_0805_2012Metric_Pad1.18x1.45mm_HandSolder
C10, C11, C12, C14, C15: 100nF; C_0805_2012Metric_Pad1.18x1.45mm_HandSolder
D1, D4: 1N4001; D_SOD-123
D2: SSR1; LED_1206_3216Metric_Pad1.42x1.75mm_HandSolder
D3: POWER_LED; LED_1206_3216Metric_Pad1.42x1.75mm_HandSolder
D5: SSR2; LED_1206_3216Metric_Pad1.42x1.75mm_HandSolder
D7: TXD; LED_1206_3216Metric_Pad1.42x1.75mm_HandSolder
D8: RXD; LED_1206_3216Metric_Pad1.42x1.75mm_HandSolder
F1: Fuse; Fuseholder_Littelfuse_100_series_5x30mm
H1, H2, H4, H5: MountingHole_Pad; MountingHole_3.2mm_M3_DIN965_Pad
J1: ACCON; TerminalBlock_Phoenix_PT-1,5-3-5.0-H_1x03_P5.00mm_Horizontal
J2: OLED 0.91; PinHeader_1x04_P2.54mm_Vertical
J3: PTC_Con; TerminalBlock_Phoenix_PT-1,5-2-5.0-H_1x02_P5.00mm_Horizontal
J4: 12V; BarrelJack_Horizontal
J5: SSROUT2; TerminalBlock_Phoenix_PT-1,5-2-5.0-H_1x02_P5.00mm_Horizontal
J6: USB_B; USB_B_OST_USB-B1HSxx_Horizontal
J7, J8, J10: PINOUT; PinHeader_1x10_P2.54mm_Vertical
J9: 12VIN; TerminalBlock_Phoenix_PT-1,5-2-5.0-H_1x02_P5.00mm_Horizontal
J11: ST7789; PinSocket_1x08_P2.54mm_Vertical
J13: JTAG10; PinHeader_2x05_P2.54mm_Vertical
K1: G3MB202PDC12; RELAY_G3MB202PDC12; PARTREV N/A
Q1, Q2: SS8550; SOT-23_Handsoldering
Q3, Q4: SS8050; SOT-23_Handsoldering
R1, R2, R4, R5, R6: 25k; R_0805_2012Metric_Pad1.20x1.40mm_HandSolder
R3: 2.5k; R_0805_2012Metric_Pad1.20x1.40mm_HandSolder
R7, R10, R14, R15, R16, R17, R19, R20, R23, R24: 10k; R_0805_2012Metric_Pad1.20x1.40mm_HandSolder
R8, R9: 16k; R_0805_2012Metric_Pad1.20x1.40mm_HandSolder
R12, R13: 4K7; R_0805_2012Metric_Pad1.20x1.40mm_HandSolder
R18, R22, R25, R26, R27, R28: 1k; R_0805_2012Metric_Pad1.20x1.40mm_HandSolder
R29, R30, R31, R32: 22k; R_0805_2012Metric_Pad1.20x1.40mm_HandSolder
RA1: 25k; R_0805_2012Metric_Pad1.20x1.40mm_HandSolder
RB1: 25k; R_0805_2012Metric_Pad1.20x1.40mm_HandSolder
SW2: RST; SW_Push_1P1T_NO_6x6mm_H9.5mm
SW3: IO0; SW_Push_1P1T_NO_6x6mm_H9.5mm
SW4: D; SW_Push_1P1T_NO_6x6mm_H9.5mm
SW5: U; SW_Push_1P1T_NO_6x6mm_H9.5mm
SW6: L; SW_Push_1P1T_NO_6x6mm_H9.5mm
SW7: R; SW_Push_1P1T_NO_6x6mm_H9.5mm
TH1: PT100; TO-92-2_Horizontal2
U1: TL431LP; TO-92_Inline_Wide
U2: TL074; SOIC-14_3.9x8.7mm_P1.27mm
U3: AMS1117-3.3; SOT-223-3_TabPin2
U4: L7805; TO-220F-3_Horizontal_TabDown
U6: ESP32-WROOM-32D
U7: CH340C; SOIC-16_3.9x9.9mm_P1.27mm

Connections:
+2V5: R1.1, R2.1, U1.1 (REF), U1.3 (K)
+3.3V: C2.1, C9.1, C10.1, C12.1, C13.1, J7.1, J10.1, J11.2, J11.8, J13.1 (VTref), R12.2, R13.2, R16.1, R17.1, R19.1, R20.1, R26.1, R27.1, R28.1, U3.2 (VO), U6.2 (VDD), U7.4 (V3), U7.16 (VCC)
+5V: C7.1, C8.1, D1.2 (A), D4.2 (A), J2.3, J6.1 (VBUS), J8.1, R1.2, R22.2, U2.4 (V+), U3.3 (VI), U4.3 (OUT)
+12V: C6.1, J4.1, J9.1, U4.1 (IN)
/ADC1_CH7: J10.10, U6.7 (IO35)
/DTR: Q4.2 (E), R7.2, U7.13 (~DTR)
/EN: C11.1, C14.1, J13.10 (~RESET), Q3.3 (C), R28.2, SW2.2, U6.3 (EN)
/I2C_SCL: J2.2, J7.6, R13.1, U6.28 (IO17)
/I2C_SDA: J2.1, J7.5, R12.1, U6.27 (IO16)
/IN1: C18.1, J10.6, R29.1, U6.12 (IO27)
/IN2: C16.1, J10.5, R30.1, U6.11 (IO26)
/IN3: C17.1, J10.4, R31.1, U6.10 (IO25)
/IN4: C19.1, J7.10, R32.1, U6.36 (IO22)
/IO0: C15.1, J8.3, Q4.3 (C), SW3.2, U6.25 (IO0)
/LCD_CS: J8.5, J11.7, U6.24 (IO2)
/LCD_DC: J10.8, J11.6, U6.9 (IO33)
/LCD_RST: J10.7, J11.5, U6.8 (IO32)
/MTCK: J8.10, J13.4 (SWCLK/TCK), U6.16 (IO13)
/MTDI: J8.9, J13.8 (NC/TDI), U6.14 (IO12)
/MTDO: J7.4, J13.6 (SWO/TDO), U6.23 (IO15)
/MTMS: J7.3, J13.2 (SWDIO/TMS), U6.13 (IO14)
/PT100: J10.9, U2.13 (-), U2.14, U6.6 (IO34)
/PT100Voltage: J3.1, R3.1, R8.2, TH1.1, U2.5 (+)
/RTS: Q3.2 (E), R10.2, U7.14 (~RTS)
/RXD: D8.1 (K), J8.4, U6.35 (TXD0/IO1), U7.3 (RXD)
/SSRIN1: J8.7, R15.1, U6.26 (IO4)
/SSRIN2: J7.9, R23.1, U6.33 (IO21)
/TXD: D7.1 (K), J8.6, U6.34 (RXD0/IO3), U7.2 (TXD)
/VSPI_CLK: J7.7, J11.3, U6.30 (IO18)
/VSPI_CS0: J8.8, U6.29 (IO5)
/VSPI_D: J10.3, J11.4, U6.37 (IO23)
/VSPI_Q: J7.8, U6.31 (IO19)
AC: F1.1, J1.1
GND: C2.2, C3.2, C6.2, C7.2, C8.2, C9.2, C10.2, C11.2, C12.2, C13.2, C14.2, C15.2, C16.2, C17.2, C18.2, C19.2, D2.1 (K), D3.1 (K), D5.1 (K), J2.4, J3.2, J4.2, J4.3, J5.2, J6.4 (GND), J6.5 (Shield), J7.2, J8.2, J9.2, J10.2, J11.1, J13.3 (GND), J13.5 (GND), J13.9 (GNDDetect), K1.4 (-), R5.1, RB1.1, SW2.1, SW3.1, SW4.1, SW5.1, SW6.1, SW7.1, TH1.2, U1.2 (A), U2.11 (V-), U3.1 (GND), U4.2 (GND), U6.1 (GND), U6.15 (GND), U6.38 (GND), U6.39 (GND), U7.1 (GND)
unnamed: C1.2, R8.1, R9.2
unnamed: D1.1 (K), Q1.2 (E), R14.2
unnamed: D2.2 (A), R18.1
unnamed: D3.2 (A), R22.1
unnamed: D4.1 (K), Q2.2 (E), R24.2
unnamed: D5.2 (A), R25.1
unnamed: D7.2 (A), R26.2
unnamed: D8.2 (A), R27.2
unnamed: J1.3, K1.1 (L1)
unnamed: J5.1, Q2.3 (C), R25.2
unnamed: J6.3 (D+), U7.5 (UD+)
unnamed: J6.2 (D-), U7.6 (UD-)
unnamed: K1.3 (+), Q1.3 (C), R18.2
unnamed: F1.2, K1.2 (L2)
unnamed: Q1.1 (B), R14.1, R15.2
unnamed: Q2.1 (B), R23.2, R24.1
unnamed: Q3.1 (B), R7.1
unnamed: Q4.1 (B), R10.1
unnamed: R3.2, R6.1, U2.1
unnamed: R16.2, R29.2, SW6.2
unnamed: R17.2, R30.2, SW4.2
unnamed: R19.2, R31.2, SW5.2
unnamed: R20.2, R32.2, SW7.2
unnamed: R2.2, R4.1, U2.3 (+)
unnamed: R5.2, R6.2, U2.2 (-)
unnamed: R4.2, U2.6 (-), U2.7
unnamed: C3.1, R9.1, U2.10 (+)
unnamed: RA1.1, RB1.2, U2.9 (-)
unnamed: C1.1, RA1.2, U2.8, U2.12 (+)

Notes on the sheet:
Sallen-Key Filter http://sim.okawa-denshi.jp/en/OPstool.php
Reference Design Schematic: ESP32-DevKit V4 https://dl.espressif.com/dl/schematics/esp32_devkitc_v4-sch.pdf
SUPPLY VOLTAGE
JTAG 10PIN
Output is limited by output range, which is typically 1.5 V to 10.5 V, or VCC- + 1.5 V to VCC+ - 1.5 V.
Pinout Image https://electropeak.com/learn/wp-content/uploads/2021/02/ 1-3-Inch-240x240-IPS-SPI-HD-LCD-Full-Color-Display-OLED-Module-Pin.jpg
ESP32 WROOM
PT100-PREAMP
DISPLAY
Pins SCK/CLK, SDO/SD0, SDI/SD1, SHD/SD2, SWP/SD3 and SCS/CMD, namely, GPIO6 to GPIO11 are connected to the integrated SPI flash integrated on the module and are not recommended for other uses.
TL431 Vo=(1+R1/R2)*vref which: vref approx 2.5v R1=0 R2=~
Target Temp for PT100 is Less 400*C, Based on Resistance table its about 250ohm
PINOUT
Current Source 1mA
JTAG Debugging, With OpenOCD https://docs.espressif.com/projects/esp-idf/en/ latest/esp32/api-guides/jtag-debugging/index.html
SPI Terminology in ESP32 The spi_master driver uses the following terms: Host: The SPI peripheral inside the ESP32 initiating the SPI transmissions. One of SPI, HSPI or VSPI. (For now, only HSPI or VSPI are actually supported in the driver; it will support all 3 peripherals somewhere in the future.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
LCD_BACKLIGHT
USB2SERIAL
INPUT SWITCH
SSR OUTPUT

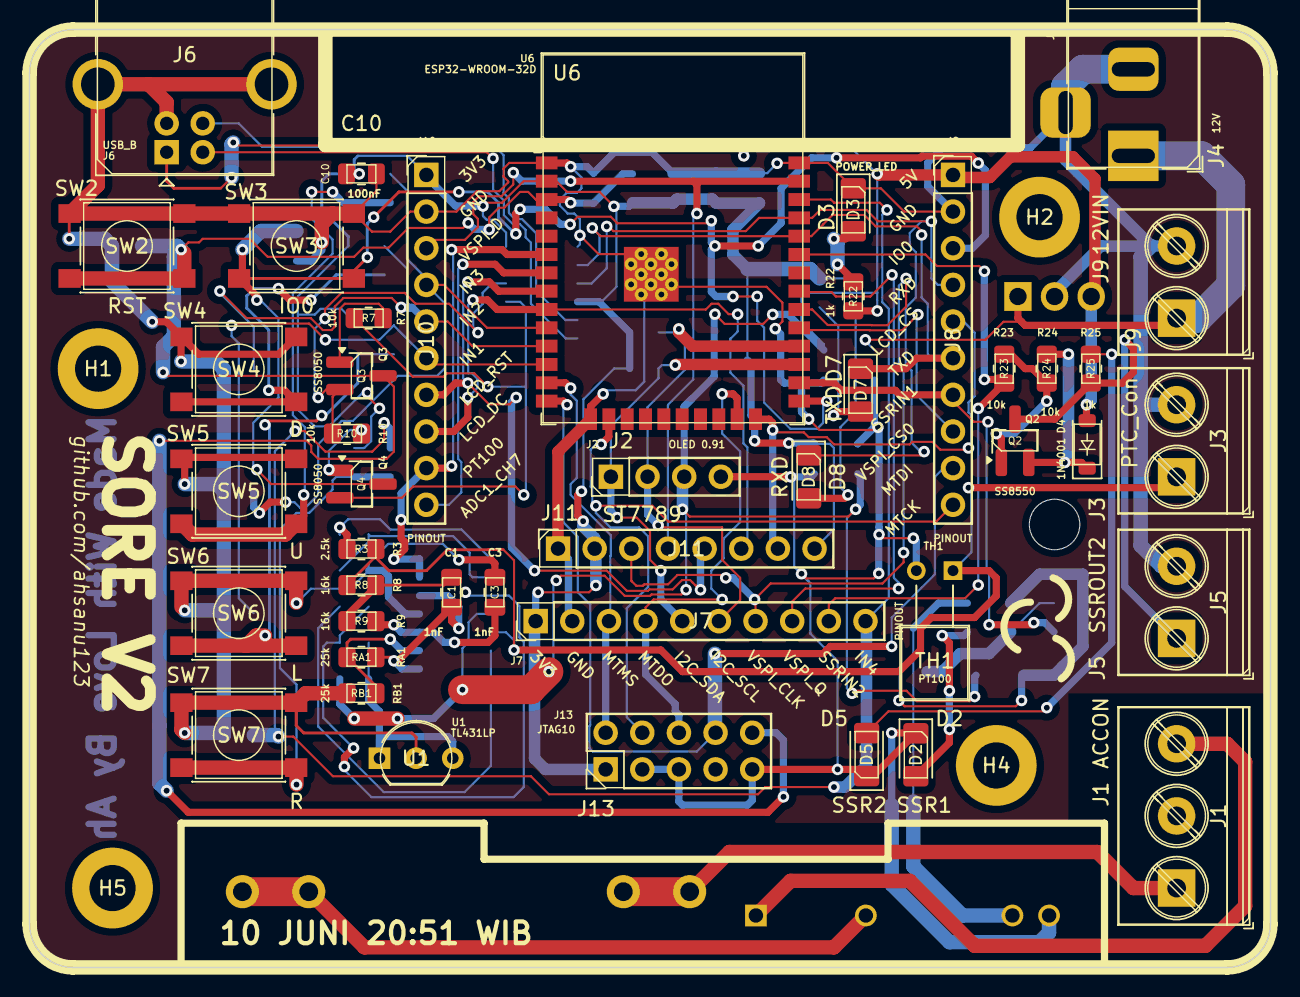
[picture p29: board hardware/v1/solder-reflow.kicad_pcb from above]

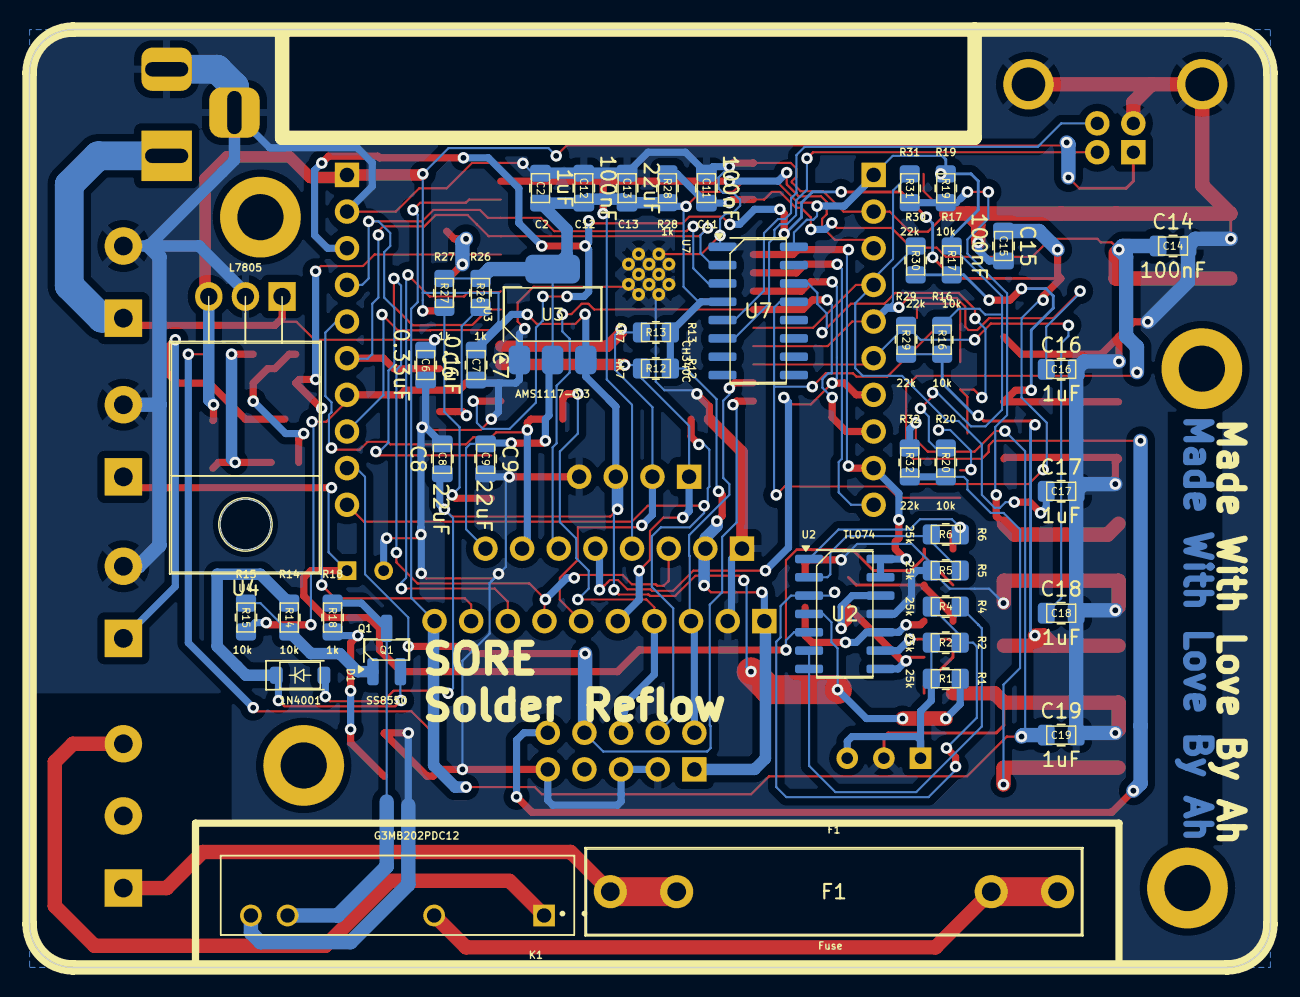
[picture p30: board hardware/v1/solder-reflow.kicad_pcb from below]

Board: 2 copper layers, 86.0 x 65.0 mm, 91 parts (43 on the bottom side), 63 nets.

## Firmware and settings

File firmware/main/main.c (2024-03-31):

// Copyright 2018-2025 Espressif Systems (Shanghai) PTE LTD
//
// Licensed under the Apache License, Version 2.0 (the "License");
// you may not use this file except in compliance with the License.
// You may obtain a copy of the License at
//
//     http://www.apache.org/licenses/LICENSE-2.0
//
// Unless required by applicable law or agreed to in writing, software
// distributed under the License is distributed on an "AS IS" BASIS,
// WITHOUT WARRANTIES OR CONDITIONS OF ANY KIND, either express or implied.
// See the License for the specific language governing permissions and
// limitations under the License.

#include "esp_log.h"
#include "freertos/FreeRTOS.h"
#include "freertos/queue.h"
#include "freertos/task.h"
#include <stdio.h>
#include <stdlib.h>
#include <string.h>

#include "driver/uart.h"

static const char *TAG = "uart_events";

#define EX_UART_NUM UART_NUM_0

#define BUF_SIZE (1024)
#define RD_BUF_SIZE (BUF_SIZE)
static QueueHandle_t uart0_queue;

static void uart_event_task(void *pvParameters) {
  uart_event_t event;
  uint8_t *dtmp = (uint8_t *)malloc(RD_BUF_SIZE);

  for (;;) {
    // Waiting for UART event.
    uart_write_bytes(EX_UART_NUM, (const char *)TAG, strlen(TAG));
    if (xQueueReceive(uart0_queue, (void *)&event,
                      (portTickType)portMAX_DELAY)) {

      bzero(dtmp, RD_BUF_SIZE);
      ESP_LOGI(TAG, "uart[%d] event:", EX_UART_NUM);

      switch (event.type) {
      // Event of UART receving data
      // We'd better handler data event fast, there would be much more data
      // events than other types of events. If we take too much time on data
      // event, the queue might be full.
      case UART_DATA:
        ESP_LOGI(TAG, "[UART DATA]: %d", event.size);
        uart_read_bytes(EX_UART_NUM, dtmp, event.size, portMAX_DELAY);
        ESP_LOGI(TAG, "[DATA EVT]:");
        uart_write_bytes(EX_UART_NUM, (const char *)dtmp, event.size);
        break;

      // Event of HW FIFO overflow detected
      case UART_FIFO_OVF:
        ESP_LOGI(TAG, "hw fifo overflow");
        // If fifo overflow happened, you should consider adding flow control
        // for your application. The ISR has already reset the rx FIFO, As an
        // example, we directly flush the rx buffer here in order to read more
        // data.
        uart_flush_input(EX_UART_NUM);
        xQueueReset(uart0_queue);
        break;

      // Event of UART ring buffer full
      case UART_BUFFER_FULL:
        ESP_LOGI(TAG, "ring buffer full");
        // If buffer full happened, you should consider encreasing your buffer
        // size As an example, we directly flush the rx buffer here in order to
        // read more data.
        uart_flush_input(EX_UART_NUM);
        xQueueReset(uart0_queue);
        break;

      case UART_PARITY_ERR:
        ESP_LOGI(TAG, "uart parity error");
        break;

      // Event of UART frame error
      case UART_FRAME_ERR:
        ESP_LOGI(TAG, "uart frame error");
        break;

      // Others
      default:
        ESP_LOGI(TAG, "uart event type: %d", event.type);
        break;
      }
    }
  }

  free(dtmp);
  dtmp = NULL;
  vTaskDelete(NULL);
}

void app_main() {
  // Configure parameters of an UART driver,
  // communication pins and install the driver
  uart_config_t uart_config = {.baud_rate = 74880,
                               .data_bits = UART_DATA_8_BITS,
                               .parity = UART_PARITY_DISABLE,
                               .stop_bits = UART_STOP_BITS_1,
                               .flow_ctrl = UART_HW_FLOWCTRL_DISABLE};
  uart_param_config(EX_UART_NUM, &uart_config);

  // Install UART driver, and get the queue.
  uart_driver_install(EX_UART_NUM, BUF_SIZE * 2, BUF_SIZE * 2, 100,
                      &uart0_queue, 0);

  // Create a task to handler UART event from ISR
  xTaskCreate(uart_event_task, "uart_event_task", 2048, NULL, 12, NULL);
}

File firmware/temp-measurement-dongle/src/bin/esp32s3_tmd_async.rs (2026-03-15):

#![no_std]
#![no_main]
#![deny(
    clippy::mem_forget,
    reason = "mem::forget is generally not safe to do with esp_hal types, especially those \
    holding buffers for the duration of a data transfer."
)]
#![deny(clippy::large_stack_frames)]

use alloc::boxed::Box;
use defmt::info;
use defmt::println;
use embassy_executor::Spawner;
use embassy_futures::select::{Either4, select4};
use embassy_sync::blocking_mutex::raw::CriticalSectionRawMutex;
use embassy_sync::pubsub::PubSubChannel;
use embassy_sync::pubsub::WaitResult;
use embassy_time::Timer;
use embedded_hal_bus::spi::ExclusiveDevice;
use esp_hal::clock::CpuClock;
use esp_hal::delay::Delay;
use esp_hal::dma::{DmaRxBuf, DmaTxBuf};
use esp_hal::dma_buffers;
use esp_hal::gpio::{Input, InputConfig, Level, Output, OutputConfig, Pull};
use esp_hal::spi::Mode;
use esp_hal::spi::master::Config;
use esp_hal::spi::master::Spi;
use esp_hal::time::Rate;
use esp_hal::timer::timg::TimerGroup;
use mipidsi::options::{ColorOrder, Orientation, Rotation};
use slint::ComponentHandle;
use slint::platform::Key;
use slint::platform::WindowEvent;
use slint::platform::software_renderer::{MinimalSoftwareWindow, RepaintBufferType};
use static_cell::StaticCell;
use tmd::platforms::esp32s3_async::backend::Esp32AsyncBackend;
use tmd::platforms::esp32s3_async::draw_buffer::DrawBuffer;
use tmd_ui::TmdApp;
use {esp_backtrace as _, esp_println as _};

extern crate alloc;

// This creates a default app-descriptor required by the esp-idf bootloader.
// For more information see: <https://docs.espressif.com/projects/esp-idf/en/stable/esp32/api-reference/system/app_image_format.html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>
esp_bootloader_esp_idf::esp_app_desc!();

const MY_TASK_POOL_SIZE: usize = 2;

static INTERFACE_BUFFER: StaticCell<[u8; 312]> = StaticCell::new();

static DISPLAY_HEIGHT: usize = 172;
static DISPLAY_WIDTH: usize = 320;

#[derive(Clone)]
pub enum KeyEvent {
    Up,
    Right,
    Down,
    Left,
}

static PUBSUB_INPUT: PubSubChannel<CriticalSectionRawMutex, KeyEvent, 4, 2, 1> =
    PubSubChannel::<CriticalSectionRawMutex, KeyEvent, 4, 2, 1>::new();

#[allow(
    clippy::large_stack_frames,
    reason = "it's not unusual to allocate larger buffers etc. in main"
)]
#[esp_rtos::main]
async fn main(spawner: Spawner) {
    esp_alloc::heap_allocator!(#[esp_hal::ram(reclaimed)] size: 73744);

    let config = esp_hal::Config::default().with_cpu_clock(CpuClock::_80MHz);
    let peripherals = esp_hal::init(config);

    let timg0 = TimerGroup::new(peripherals.TIMG0);
    esp_rtos::start(timg0.timer0);

    let input1 = peripherals.GPIO17;
    let input2 = peripherals.GPIO18;
    let input3 = peripherals.GPIO19;
    let input4 = peripherals.GPIO20;

    let lcd_dc = peripherals.GPIO15;
    let lcd_cs = peripherals.GPIO10;
    let lcd_rst = peripherals.GPIO14;
    let lcd_blk = peripherals.GPIO16;

    let scl_mosi = peripherals.GPIO13;
    let scl_sck = peripherals.GPIO12;
    let scl_miso = peripherals.GPIO11;

    let dma_channel = peripherals.DMA_CH0;

    let input1 = Input::new(input1, InputConfig::default().with_pull(Pull::Up));
    let input2 = Input::new(input2, InputConfig::default().with_pull(Pull::Up));
    let input3 = Input::new(input3, InputConfig::default().with_pull(Pull::Up));
    let input4 = Input::new(input4, InputConfig::default().with_pull(Pull::Up));

    let lcd_cs = Output::new(lcd_cs, Level::Low, OutputConfig::default());
    let lcd_dc = Output::new(lcd_dc, Level::Low, OutputConfig::default());
    let lcd_rst = Output::new(lcd_rst, Level::Low, OutputConfig::default());
    let mut lcd_blk = Output::new(lcd_blk, Level::Low, OutputConfig::default());

    let (rx_buffer, rx_descriptors, tx_buffer, tx_descriptors) = dma_buffers!(2048);
    let dma_rx_buf = DmaRxBuf::new(rx_descriptors, rx_buffer).unwrap();
    let dma_tx_buf = DmaTxBuf::new(tx_descriptors, tx_buffer).unwrap();

    let spi_bus = Spi::new(
        peripherals.SPI2,
        Config::default()
            .with_frequency(Rate::from_mhz(60))
            .with_mode(Mode::_0),
    )
    .unwrap()
    .with_sck(scl_sck)
    .with_mosi(scl_mosi)
    .with_miso(scl_miso)
    .with_dma(dma_channel)
    .with_buffers(dma_rx_buf, dma_tx_buf);

    let interface_buffer = INTERFACE_BUFFER.init([0u8; 312]);

    let mut delay = Delay::new();
    let spi_device = ExclusiveDevice::new(spi_bus, lcd_cs, delay).unwrap();

    let di = mipidsi::interface::SpiInterface::new(spi_device, lcd_dc, interface_buffer);

    let st7789 = mipidsi::Builder::new(tmd::display_models::st7789_modified::ST7789, di)
        .display_size(DISPLAY_WIDTH as u16, DISPLAY_HEIGHT as u16)
        .orientation(Orientation::new().rotate(Rotation::Deg270))
        .color_order(ColorOrder::Rgb)
        .display_offset(34, 340)
        .invert_colors(mipidsi::options::ColorInversion::Inverted)
        .reset_pin(lcd_rst)
        .init(&mut delay)
        .expect("fail to build display st7789");

    let mut draw_buffer = DrawBuffer::new(st7789);

    let window = MinimalSoftwareWindow::new(RepaintBufferType::ReusedBuffer);
    window.set_size(slint::PhysicalSize::new(
        DISPLAY_WIDTH as u32,
        DISPLAY_HEIGHT as u32,
    ));

    let backend = Box::new(Esp32AsyncBackend::new(window.clone()));
    slint::platform::set_platform(backend).expect("fail when set platform");

    info!("slint gui setup complete");

    lcd_blk.set_high();

    let tmd_app = TmdApp::new().expect("cant create Tmb Application");
    tmd_app.show().expect("unable to show tmb_app");

    spawner
        .spawn(button_task(input1, input2, input3, input4))
        .expect("fail to spawn button_task");

    let mut sub = PUBSUB_INPUT
        .subscriber()
        .expect("fail to make subscribtion");

    loop {
        slint::platform::update_timers_and_animations();

        window.draw_if_needed(|renderer| {
            info!("render by line!");
            renderer.render_by_line(&mut draw_buffer);
        });

        // TODO: simplify this
        if let Some(wait_result) = sub.try_next_message() {
            match wait_result {
                WaitResult::Lagged(amount) => println!("lag {} message", amount),
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

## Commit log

2024-03-01 staged finished schematic v1
    [matchedBiasTransistorSim.kicad_sch, solder-reflow.kicad_pcb, solder-reflow.kicad_sch]
2024-03-01 finish pcb layout
    add a backup zip
    [EC11_Rotary_Encoder_Switched.step, G3MB-202P-DC12--3DModel-STEP-56544.STEP, G3MB202PDC12.step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]
2024-03-06 finishing up routing and make a schematic pdf output
    [EC11_Rotary_Encoder_Switched.step, G3MB-202P-DC12--3DModel-STEP-56544.STEP, G3MB202PDC12.step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]
2024-03-06 rotate wemos d1 mini
    [solder-reflow.kicad_pcb]
2024-03-07 route rotated wemos and make order to jlc pcb
    [solder-reflow-B_Adhesive.gbr, solder-reflow-B_Courtyard.gbr, solder-reflow-B_Cu.gbr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]
2024-03-31 update value of one resistor
    [solder-reflow.csv, solder-reflow.kicad_pcb]
2024-03-31 copied uart example from esp8266 repo
2024-04-04 adding ssd1306 old library and add rotary encoder header
2024-04-05 [5-4-1909] adding i2c and lcdgfx back to repo, success to build
2024-04-12 [12-4-1911] adding really bad toggle button functionality
2024-06-04 [4-6-0739] add revision feature
    [solder-reflow.kicad_pcb, solder-reflow.kicad_sch]
2024-06-04 [5-6-0014] adding several io connection
    [solder-reflow.kicad_sch]
2024-06-05 [5-6-0703] adding st7789 schematic
    [solder-reflow.kicad_sch]
2024-06-05 [6-6-0359] finish first revision, need to review
    [solder-reflow.kicad_sch]
2024-06-06 [6-7-1245] finish first layout, need to review
    [solder-reflow.kicad_pcb, solder-reflow.kicad_sch]
2024-06-08 [8-06-0716] finish up layout plus adding several random graphic
    [USB-B-S-F-B-TH.stp, solder-reflow-BOM.csv, solder-reflow.kicad_pcb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]
2024-06-08 [8-06-1357] finish routing, next do second review
    [solder-reflow.kicad_pcb]
2024-06-08 add back button
2024-06-10 [10-06-2138] tune silkscreen and track width
    [solder-reflow.kicad_pcb]
2024-06-15 [15-06-1731] adding gerber
    [solder-reflow.kicad_pcb]
2024-06-15 [15-06-2201] update readme and add schematic svg
    [solder-reflow.kicad_pcb]
2024-06-15 update schematic svg background color
2024-07-14 update firmware to version 2
    [1.54 TFT IPS - 12P - Flat Flush Mount - With Glass.cfg, 1.54 TFT IPS - 12P - Flat Flush Mount.stp, 1.54 TFT IPS - 12P - Flat Mount - With Glass.cfg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]
2024-07-22 copied adc continuous from esp32 exampel
2024-07-22 add some adc definition
2024-07-23 [23-07-24] add ADCDevice class to simplify adc initialization
2024-08-29 add Gpio Device class
2024-08-30 add new adc class, still not work as expected
2024-09-02 adc queue worked, plot still noisy, does plot really look like this
2024-09-14 add adc reading with little conversion, still not correctly working
2024-09-15 lvgl esp32 port compiled but trigering watchdog, still investigating
2024-10-05 try to create input device (button) still fail
2024-10-06 lvgl input button worked!!, need to tweak
2024-10-06 simple button navigation worked!!!
2024-11-03 [10-30-2007] sampling data from heater
    move sampled data into new folder
    Update README.md
    Update README.md
    Update README.md
    [dataa2.csv]
2024-11-09 [11-03-1414] playing with PID constant
    update data
    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
2025-06-11 [06-11-2010] remove lvgl v1 and v2 firmware
    [case.3mf, dataa2.csv, doxygen.cfg]
2025-06-11 [06-11-2101] scafold esp project with embassy and defmt, use esp-generate
    esp-generate --chip esp32 -o alloc -o embassy -o defmt -o unstable-hal
    Sore-v3
    [main.rs]
2025-09-13 chore: duplicating v1 to make v3
    [1.54 TFT IPS - 12P - Flat Flush Mount - With Glass.cfg, 1.54 TFT IPS - 12P - Flat Flush Mount.stp, 1.54 TFT IPS - 12P - Flat Mount - With Glass.cfg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]
2025-09-13 feat: start creating schematic with esp32-s3 soc
    [solder-reflow.kicad_sch]
2025-09-14 feat: finish basic schematic, need to re-check
    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
    [solder-reflow.kicad_sch]
2025-09-14 feat: basic board layout finished
    [solder-reflow.kicad_pcb, solder-reflow.kicad_sch]
2025-09-14 feat: routing part 1
    [solder-reflow.kicad_pcb]
2025-10-04 feat: routing part 2
    [solder-reflow.kicad_pcb, solder-reflow.kicad_sch]
2025-12-04 feat: attempt to finish routing
    [solder-reflow.kicad_pcb, solder-reflow.kicad_sch]
2025-12-04 feat: change to use esp32-s3 tempel
    [solder-reflow.kicad_pcb, solder-reflow.kicad_sch]
2026-01-09 feat: finish routing v3 prototype 1
    [solder-reflow.kicad_pcb, solder-reflow.kicad_sch]
2026-02-02 feat: update schematic svg
    [solder-reflow.kicad_pcb, solder-reflow.kicad_sch]
2026-02-02 feat: add led indicator
    [solder-reflow.kicad_pcb, solder-reflow.kicad_sch]
2026-03-12 feat: create esp32 tmd from slint embedded sample project
2026-03-14 feat: slint with esp32s3 async poc is working
2026-03-14 feat: copying printer demo
2026-03-17 chore: remove gerber
    [solder-reflow-B_Adhesive.gbr, solder-reflow-B_Courtyard.gbr, solder-reflow-B_Cu.gbr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]

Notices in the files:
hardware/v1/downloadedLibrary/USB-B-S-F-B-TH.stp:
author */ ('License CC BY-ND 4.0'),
